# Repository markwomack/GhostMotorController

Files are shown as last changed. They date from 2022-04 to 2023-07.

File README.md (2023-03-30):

# Ghost Motor Controller
<p>The Ghost Motor Controller is currently a proof-of-concept project that is creating motor controller hardware and software to manage two BLDC hoverboard/eScooter motors with 3-phase motor encoders. The goal is to use this motor controller as part of a mobile, differential drive robot, and to have a design that can eventually be reused with different underlying hardware and motors. The parameters of the project are to use as many 'off-the-shelf' parts as possible and as few custom designed parts. This is where the project name comes from: at the end of the day we are just putting a sheet over a collection of parts and calling it a motor controller. Custom PCBs are allowed since maintaining breadboards and/or protoboards in a robot can be cumbersome and require more room than desired or needed. However, much of the PCB design is (currently) integrating existing break out boards, mostly from Pololu and Sparkfun.</p>

## Status
<p>Ghost is currently in the 'proof-of-concept' phase. Most of the time thus far has been spent choosing the initial set of parts, getting a power system in place to support the parts, and designing the first version of circuitry that will make up the motor controller. The power system, motors, and a control circuit has been designed and tested. A custom PCB has been designed and will be integrated with the test system soon.</p>

## Hardware
Instead of creating a custom circuit to control the motors, an existing eScooter controller is being used. But since this controller doesn't have a programmatic interface, a microcontroller circuit is being designed. Basically a controller of a controller. This is the Ghost Motor Controller. The hardware will support I2C, 3 RC channel inputs, and a serial port for debugging output.

## Software
The Ghost Motor Controller will provide an API accessible through I2C. Using this API the user will be able to set/get configuration and set/get information and actions on the motors and associated encoders. Everything one needs to control the motors on a mobile, differential drive robot will be provided. It will be very similar to existing APIs for other popular controllers, like the RoboClaw.

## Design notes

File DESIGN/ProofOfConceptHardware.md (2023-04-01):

# Proof of Concept Hardware (work in progress)
<p>For the proof of concept the parts below were used. If building your own version you can use
  these same parts or substitute different parts for anything in the 'Motor and Power' category
  as long as it conforms to the following requirements:</p>
  
  - The motors must be 3 phase and provide encoder signals that can be connected to the 3.3v
    Teensy 4.0 (using a 5v->3.3v logic converter, if needed, is acceptable).
  - The BLDC motor controllers must be compatible with the chosen motors and must allow for the
    speed to be set via a PWM signal.
  - Proper voltage must be provided to the motors, the motorcontrollers, and the Teensy 4.0.
  - The [36v->5v step-down regulator](https://www.amazon.com/dp/B07YCQTSXQ) is used for intial
    voltage conversion, and a second, smaller [5v step-down regulator](https://www.pololu.com/product/4941)
    is used for added protection.

<p>Substituting a different microcontroller will most likely require major reworking of the code,
  and so it is recommended that the Teensy 4.0 be used and not substituted. YMMV.</p>

## Motor and Power
  - 2 - [12" scooter/ebike BLDC motors](https://www.amazon.com/dp/B08ZXYND7G)
  - 2 - [BLDC motor controllers](https://www.amazon.com/RioRand-6-60V-Brushless-Electric-Controller/dp/B087M2378D)
  - 1 - [36v ebike lithium ion battery](https://www.amazon.com/dp/B08FWRZYJ3)
  - 1 - [Battery Disconnect Switch](https://www.amazon.com/dp/B08YXGXW2W)
  - 1 - [Inline Fuse Holder](https://www.amazon.com/dp/B081DHT8Y7)
  - 2 - [24v DC regulator](https://www.amazon.com/gp/product/B098D8HMJ9)
  - 1 - [5v DC step-down regulator](https://www.amazon.com/dp/B07YCQTSXQ)
  - 2 - [Shunt Regulator](https://www.pololu.com/product/3779)
  - 1 - [Mini Pushbutton Power Switch with Reverse Voltage Protection](https://www.pololu.com/product/2808)
  - 2 - [Big Pushbutton Power Switch with Reverse Voltage Protection](https://www.pololu.com/product/2813)
  - 1 - [3.3v step-down regulator](https://www.pololu.com/product/4940)
  - 1 - [5v step-down/up regulator](https://www.pololu.com/product/4941)
  - 1 - Diode (to prevent backflow to the power switches)
  - 1 - Momentary pushbutton

## Microcontroller
  - 1 - [Teensy 4.0](https://www.pjrc.com/store/teensy40.html)
  - 5 - [Logic Converter](https://www.sparkfun.com/products/12009)
  - 2 - [Hex Inverters with Schmitt Triggers IC chips)](https://www.digikey.com/en/products/detail/texas-instruments/SN74HC14N/277223)
  - 6 - [1000pF capacitors](https://www.digikey.com/en/products/detail/vishay-beyschlag-draloric-bc-components/A102K15X7RF5TAA/2356716)
  - 1 - Momentary pushbutton

## Miscellaneous
  - [Wire connectors](https://www.amazon.com/dp/B0882TNS73)
  - [12 AWG wire](https://www.amazon.com/dp/B01ABOPMEI)

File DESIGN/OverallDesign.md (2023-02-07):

# Overall Design
<p>Simply stated, the goal of this project is to create a motor controller that can
control two scooter Brushless DC (BLDC) motors and that can be used in robotic projects in
replacement of more typical motors and motor controllers. Scooter BLDC motors, due
to their design, can handle large loads (on the order of a grown adult) and can
provide lots of torque. These features make them very ideal for many robotic
applications.</p>

<p>BLDC motors have been around forever, and are a staple of most 
robotic projects, especially mobile robots. BLDC motors used on scooters have been
on the scene more recently but have gained in popularity and availability. One can
find many different models on Amazon and scooter supply websites. But using them
in a robotics project poses some difficulty.</p>

<p>Scooter BLDC motors use a 3-phase design for the motor, not just the simple two
wire configuration used in most robotic motors. In addition, while most scooter
motors have encoders built in, they are three encoders to match the 3-phases.
Two sensor, quadrature encoder support doesn't work. Both of these major differences
mean that none of the normal robotic motor controllers can be used to control scooter
motors.</p>

<p>While the usual stable of robotic motor controllers can't be used for scooter
BLDC motors, there are motor controllers that exist to control them. Scooters
obviously need some component to manage the motor speed, braking, and stopping
as the user drives the scooter around. These controllers are fairly simple in
design, providing for the 3-phase power signals and using the encoders to determine
wheel position and how to control the motor. As part of this project, one could design
and build such a controller from scratch, but instead we have opted to incorporate the
existing simple controller in the design. Doing so allows the builder to swap out the
simple controller to better match the power and motor requirements of their project.
As long as the replacement controller uses the same required interface for the power
and encoders, it should just be a matter of a drop-in replacement.</p>

<p>Similarly, the motors themselves can be swapped out as needed for the project
requirements. As long as the motor is a 3-phase motor with connections for power and
encoders, it will be compatible.</p>

<p>The real innovation will be the circuitry that encapsulates the simple controllers
and motors. It will provide an interface to control the motors based on a popular 
motor controller protocol, the RoboClaw. It will be a motor controller of motor
controllers, so to speak. Commands to control the motors will be sent to this top
level controller (via I2C or Serial, tbd), and the top level controller will in turn
send the proper commands to the simple controllers. In addition, PID control will be
implemented, using the 3-phase encoder signals from the motors. But putting the simple
controllers and motors behind a higher-level motor controller interface, scooter BLDC
motors will be easier to incorporate into a robotics project.</p>

# References

  - [https://www.digikey.com/en/articles/how-to-power-and-control-brushless-dc-motors](https://www.digikey.com/en/articles/how-to-power-and-control-brushless-dc-motors)
  - [https://www.digikey.com/en/blog/using-bldc-hall-sensors-as-position-encoders-part-1](https://www.digikey.com/en/blog/using-bldc-hall-sensors-as-position-encoders-part-1)

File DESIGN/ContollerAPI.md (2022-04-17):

# Controller Interface/API
This document outlines the API of the controller interface that is used to control the motors.
For purposes of design we are assuming I2C is used and that there is a set of registers that
are read-only or read/write as appropriate. Setting a register affects the motorcontroller as
it uses that value to control the motors.

## Read/Write registers

  - Target speed left motor - The target speed for the left motor the PID should aim for. (units for speed, tbd)
  - P value, left motor - The P value to use for PID controller of left motor.
  - I value, left motor - The I value to use for PID controller of left motor.
  - D value, left motor - The D value to use for PID controller of left motor.
  - Target speed right motor - The target speed for the right motor the PID should aim for. (units for speed, tbd)
  - P value, right motor - The P value to use for PID controller of right motor.
  - I value, right motor - The I value to use for PID controller of right motor.
  - D value, right motor - The D value to use for PID controller of right motor.
  - Command timeout - The amount of time before the motorcontroller will stop all motors if no command is received.

## Read-Only registers

  - Current speed left motor - The current speed of the left motor.
  - Current speed right motor - The current speed of the right motor.

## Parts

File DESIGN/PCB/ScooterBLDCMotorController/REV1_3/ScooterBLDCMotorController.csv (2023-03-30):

Comment | Designator | Footprint | LCSC
M1 OUTPUT | J1 | TerminalBlock:TerminalBlock_Altech_AK300-3_P5.00mm | C5142611
RC_ENABLE | J10 | Connector_PinHeader_2.54mm:PinHeader_1x02_P2.54mm_Vertical | C5116481
TO M2 ENCODER | J11 | Connector_JST:JST_XH_B5B-XH-A_1x05_P2.50mm_Vertical | C157991
M2 INPUT | J12 | Custom:TerminalBlock_Altech_AK300-5_P5.00mm | C395854
RC CH 3 | J15 | Connector_JST:JST_XH_B3B-XH-A_1x03_P2.50mm_Vertical | C161870
TO M1 ENCODER | J2 | Connector_JST:JST_XH_B5B-XH-A_1x05_P2.50mm_Vertical | C157991
M1 INPUT | J3 | Custom:TerminalBlock_Altech_AK300-5_P5.00mm | C395854
M2 OUTPUT | J4 | TerminalBlock:TerminalBlock_Altech_AK300-3_P5.00mm | C5142611
I2C | J5 | Connector_JST:JST_XH_B2B-XH-A_1x02_P2.50mm_Vertical | C158012
TEST SWITCH | J6 | Connector_JST:JST_XH_B2B-XH-A_1x02_P2.50mm_Vertical | C158012
RC CH 1 | J7 | Connector_JST:JST_XH_B3B-XH-A_1x03_P2.50mm_Vertical | C161870
RC CH 2 | J8 | Connector_JST:JST_XH_B3B-XH-A_1x03_P2.50mm_Vertical | C161870
RC_PWR | J9 | Connector_PinHeader_2.54mm:PinHeader_1x02_P2.54mm_Vertical | C5116481
5v | POWER1 | Connector_JST:JST_XH_B2B-XH-A_1x02_P2.50mm_Vertical | C158012
SERIAL | SERIAL1 | Connector_JST:JST_XH_B2B-XH-A_1x02_P2.50mm_Vertical | C158012
SN74HC14NR | U2,U5 | Package_DIP:DIP-14_W7.62mm | C2907

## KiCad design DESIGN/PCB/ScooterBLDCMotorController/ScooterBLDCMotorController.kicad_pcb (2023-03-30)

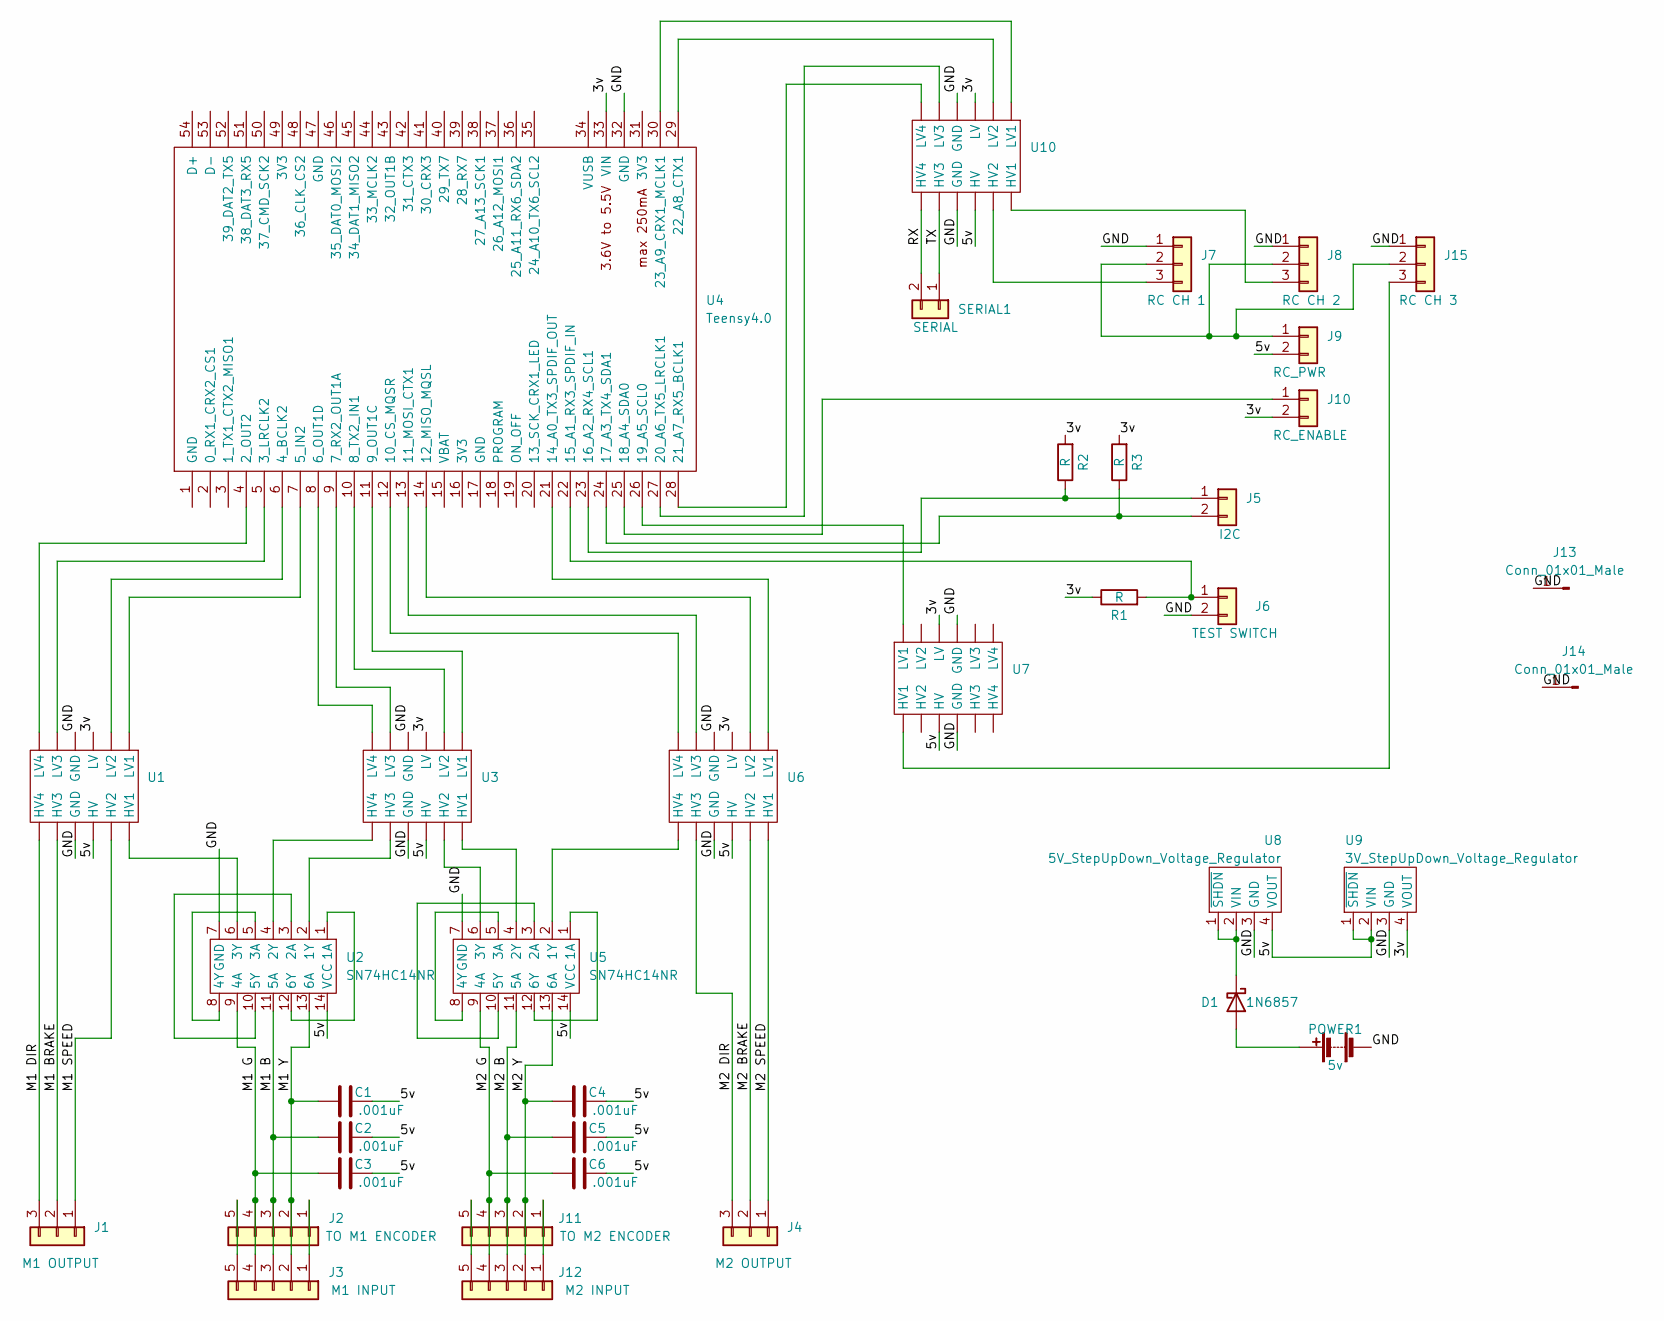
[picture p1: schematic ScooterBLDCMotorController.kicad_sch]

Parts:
C1, C2, C3, C4, C5, C6: .001uF; C_Axial_L3.8mm_D2.6mm_P7.50mm_Horizontal
D1: 1N6857; D_DO-35_SOD27_P7.62mm_Horizontal
J1: M1 OUTPUT; TerminalBlock_Altech_AK300-3_P5.00mm; LCSC C8393
J2: TO M1 ENCODER; JST_XH_B5B-XH-A_1x05_P2.50mm_Vertical; LCSC C157991
J3: M1 INPUT; TerminalBlock_Altech_AK300-5_P5.00mm; LCSC C395854
J4: M2 OUTPUT; TerminalBlock_Altech_AK300-3_P5.00mm; LCSC C8393
J5: I2C; JST_XH_B2B-XH-A_1x02_P2.50mm_Vertical; LCSC C158012
J6: TEST SWITCH; JST_XH_B2B-XH-A_1x02_P2.50mm_Vertical; LCSC C158012
J7: RC CH 1; JST_XH_B3B-XH-A_1x03_P2.50mm_Vertical; LCSC C161870
J8: RC CH 2; JST_XH_B3B-XH-A_1x03_P2.50mm_Vertical; LCSC C161870
J9: RC_PWR; PinHeader_1x02_P2.54mm_Vertical; LCSC C5116481
J10: RC_ENABLE; PinHeader_1x02_P2.54mm_Vertical; LCSC C5116481
J11: TO M2 ENCODER; JST_XH_B5B-XH-A_1x05_P2.50mm_Vertical; LCSC C157991
J12: M2 INPUT; TerminalBlock_Altech_AK300-5_P5.00mm; LCSC C395854
J13, J14: Conn_01x01_Male; PinHeader_1x01_P2.54mm_Vertical
J15: RC CH 3; JST_XH_B3B-XH-A_1x03_P2.50mm_Vertical; LCSC C161870
POWER1: 5v; JST_XH_B2B-XH-A_1x02_P2.50mm_Vertical; LCSC C158012
R1, R2, R3: R; R_Axial_DIN0204_L3.6mm_D1.6mm_P7.62mm_Horizontal
SERIAL1: SERIAL; JST_XH_B2B-XH-A_1x02_P2.50mm_Vertical; LCSC C158012
U1, U3, U6, U7, U10: Level Shifter
U2, U5: SN74HC14NR; DIP-14_W7.62mm; LCSC C2907
U4: Teensy4.0; Teensy40_sides
U8: 5V_StepUpDown_Voltage_Regulator; StepUpDown Voltage Regulator
U9: 3V_StepUpDown_Voltage_Regulator; StepUpDown Voltage Regulator

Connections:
/3v: J10.2, R1.1, R2.2, R3.2, U1.9 (LV), U3.9 (LV), U4.33 (VIN), U6.9 (LV), U7.9 (LV), U9.4 (VOUT), U10.9 (LV)
/5v: C1.2, C2.2, C3.2, C4.2, C5.1, C6.1, J9.2, U1.4 (HV), U2.14 (VCC), U3.4 (HV), U5.14 (VCC), U6.4 (HV), U7.4 (HV), U8.4 (VOUT), U9.1 (~SHDN), U9.2 (VIN), U10.4 (HV)
/GND: J6.2, J7.1, J8.1, J13.1, J14.1, J15.1, POWER1.2 (-), U1.3 (GND), U1.10 (GND), U2.7 (GND), U3.3 (GND), U3.10 (GND), U4.32 (GND), U5.7 (GND), U6.3 (GND), U6.10 (GND), U7.3 (GND), U7.10 (GND), U8.3 (GND), U9.3 (GND), U10.3 (GND), U10.10 (GND)
/M1 B: C2.1, J2.3, J3.3, U2.11 (5A)
/M1 BRAKE: J1.2, U1.2 (HV3)
/M1 DIR: J1.3, U1.1 (HV4)
/M1 G: C3.1, J2.4, J3.4, U2.9 (4A)
/M1 SPEED: J1.1, U1.5 (HV2)
/M1 Y: C1.1, J2.2, J3.2, U2.13 (6A)
/M2 B: C5.2, J11.3, J12.3, U5.11 (5A)
/M2 BRAKE: J4.2, U6.5 (HV2)
/M2 DIR: J4.3, U6.2 (HV3)
/M2 G: C6.2, J11.4, J12.4, U5.9 (4A)
/M2 SPEED: J4.1, U6.6 (HV1)
/M2 Y: C4.1, J11.2, J12.2, U5.13 (6A)
/RX: SERIAL1.2, U10.1 (HV4)
/TX: SERIAL1.1, U10.2 (HV3)
unnamed: D1.2 (A), POWER1.1 (+)
unnamed: D1.1 (K), U8.1 (~SHDN), U8.2 (VIN)
unnamed: J2.1, J3.1
unnamed: J2.5, J3.5
unnamed: J5.1, R2.1, U4.23 (16_A2_RX4_SCL1)
unnamed: J5.2, R3.1, U4.24 (17_A3_TX4_SDA1)
unnamed: J6.1, R1.2, U4.22 (15_A1_RX3_SPDIF_IN)
unnamed: J7.3, U10.5 (HV2)
unnamed: J8.3, U10.6 (HV1)
unnamed: J10.1, U4.25 (18_A4_SDA0)
unnamed: J11.1, J12.1
unnamed: J11.5, J12.5
unnamed: J7.2, J8.2, J9.1, J15.2
unnamed: J15.3, U7.6 (HV1)
unnamed: U1.6 (HV1), U2.6 (3Y)
unnamed: U1.7 (LV1), U4.7 (5_IN2)
unnamed: U1.8 (LV2), U4.6 (4_BCLK2)
unnamed: U1.11 (LV3), U4.5 (3_LRCLK2)
unnamed: U1.12 (LV4), U4.4 (2_OUT2)
unnamed: U2.1 (1A), U2.12 (6Y)
unnamed: U2.2 (1Y), U3.2 (HV3)
unnamed: U2.3 (2A), U2.10 (5Y)
unnamed: U2.4 (2Y), U3.1 (HV4)
unnamed: U2.5 (3A), U2.8 (4Y)
unnamed: U3.6 (HV1), U5.4 (2Y)
unnamed: U3.5 (HV2), U5.6 (3Y)
unnamed: U3.7 (LV1), U4.11 (9_OUT1C)
unnamed: U3.8 (LV2), U4.10 (8_TX2_IN1)
unnamed: U3.11 (LV3), U4.9 (7_RX2_OUT1A)
unnamed: U3.12 (LV4), U4.8 (6_OUT1D)
unnamed: U4.12 (10_CS_MQSR), U6.12 (LV4)
unnamed: U4.13 (11_MOSI_CTX1), U6.11 (LV3)
unnamed: U4.14 (12_MISO_MQSL), U6.8 (LV2)
unnamed: U4.21 (14_A0_TX3_SPDIF_OUT), U6.7 (LV1)
unnamed: U4.26 (19_A5_SCL0), U7.7 (LV1)
unnamed: U5.1 (1A), U5.12 (6Y)
unnamed: U5.2 (1Y), U6.1 (HV4)
unnamed: U5.3 (2A), U5.10 (5Y)
unnamed: U5.5 (3A), U5.8 (4Y)
unnamed: U4.30 (23_A9_CRX1_MCLK1), U10.7 (LV1)
unnamed: U4.29 (22_A8_CTX1), U10.8 (LV2)
unnamed: U4.27 (20_A6_TX5_LRCLK1), U10.11 (LV3)
unnamed: U4.28 (21_A7_RX5_BCLK1), U10.12 (LV4)

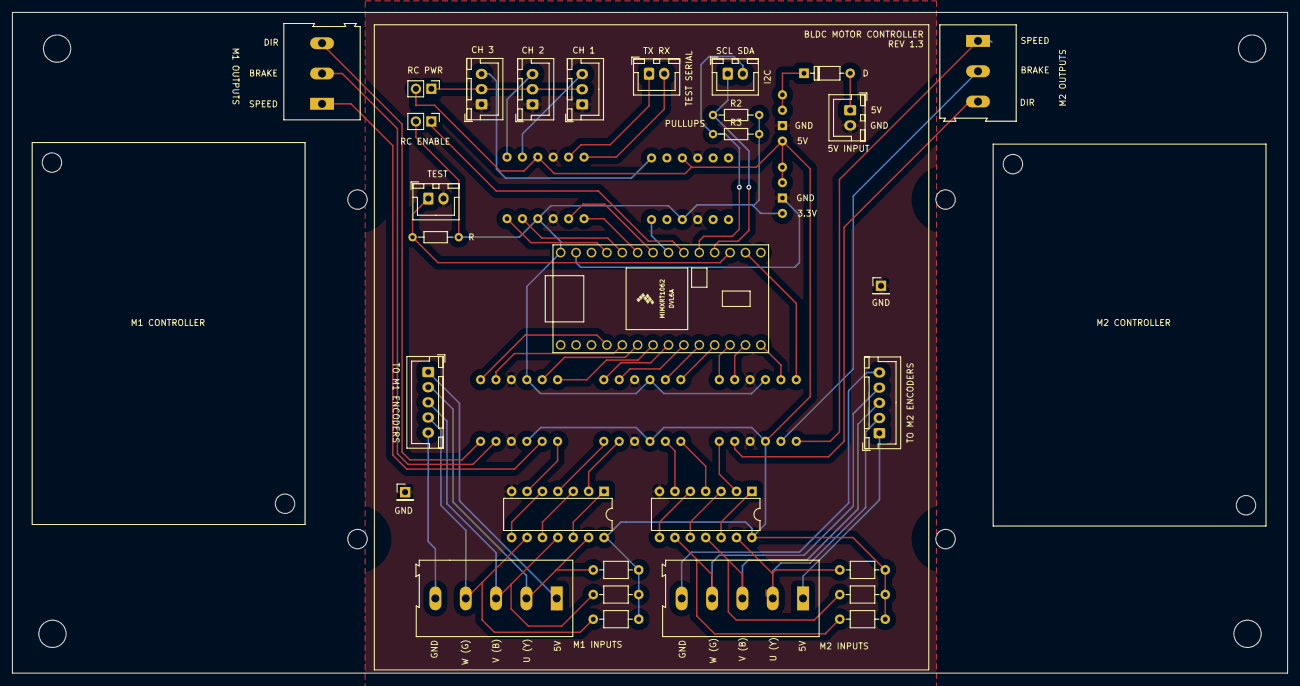
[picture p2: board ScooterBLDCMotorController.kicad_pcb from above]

Board: 2 copper layers, 210.3 x 109.0 mm, 37 parts (0 on the bottom side), 60 nets.

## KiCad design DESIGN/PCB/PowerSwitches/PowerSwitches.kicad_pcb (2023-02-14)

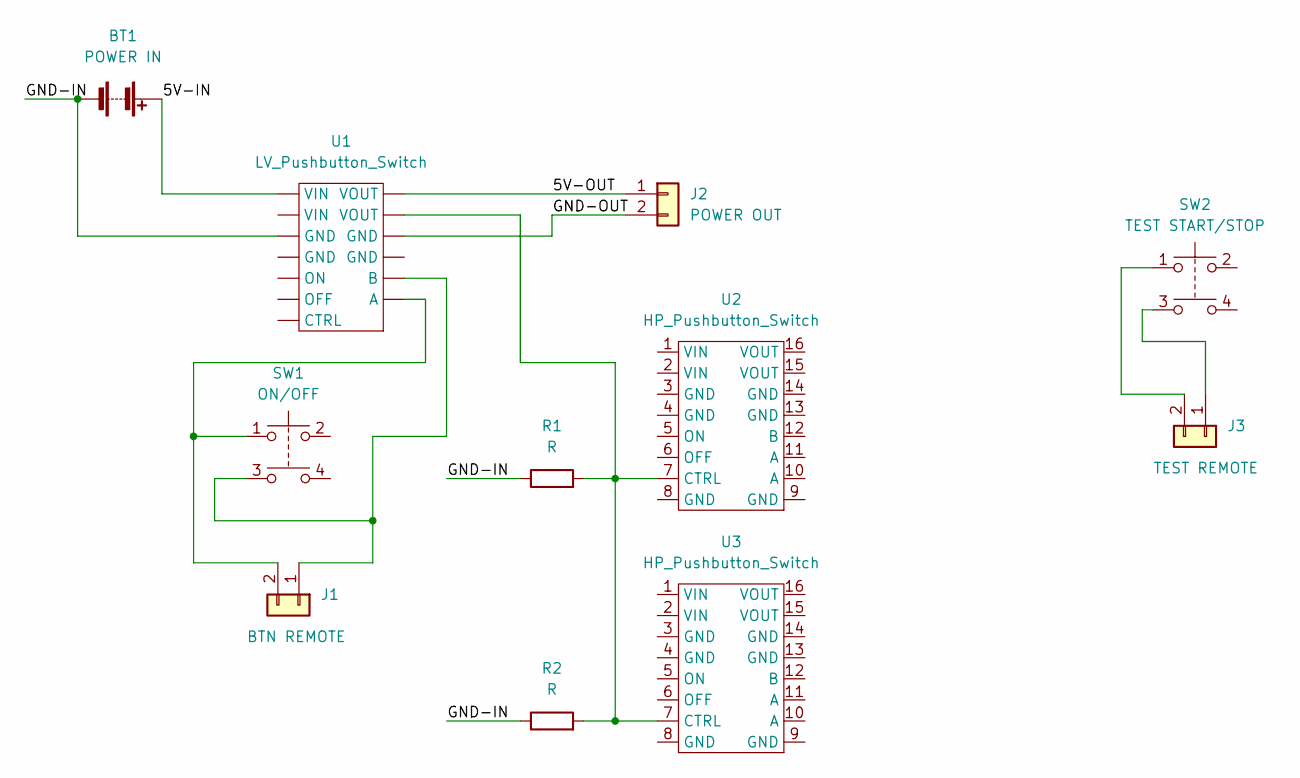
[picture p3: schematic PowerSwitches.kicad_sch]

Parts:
BT1: POWER IN; JST_XH_B2B-XH-A_1x02_P2.50mm_Vertical
J1: BTN REMOTE; JST_XH_B2B-XH-A_1x02_P2.50mm_Vertical
J2: POWER OUT; JST_XH_B2B-XH-A_1x02_P2.50mm_Vertical
J3: TEST REMOTE; JST_XH_B2B-XH-A_1x02_P2.50mm_Vertical
R1, R2: R; R_Axial_DIN0207_L6.3mm_D2.5mm_P7.62mm_Horizontal
SW1: ON/OFF; Small Dual Push Button
SW2: TEST START/STOP; Small Dual Push Button
U1: LV_Pushbutton_Switch; LV_PushButton_Switch
U2, U3: HP_Pushbutton_Switch; HV_PushButton_Switch

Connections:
/5V-IN: BT1.1 (+), U1.1 (VIN)
/5V-OUT: J2.1, U1.13 (VOUT)
/GND-IN: BT1.2 (-), R1.1, R2.1, U1.3 (GND)
/GND-OUT: J2.2, U1.11 (GND)
unnamed: J1.2, SW1.1, U1.8 (A)
unnamed: J3.2, SW2.1
unnamed: R1.2, R2.2, U1.12 (VOUT), U2.7 (CTRL), U3.7 (CTRL)
unnamed: J3.1, SW2.3
unnamed: J1.1, SW1.3, U1.9 (B)

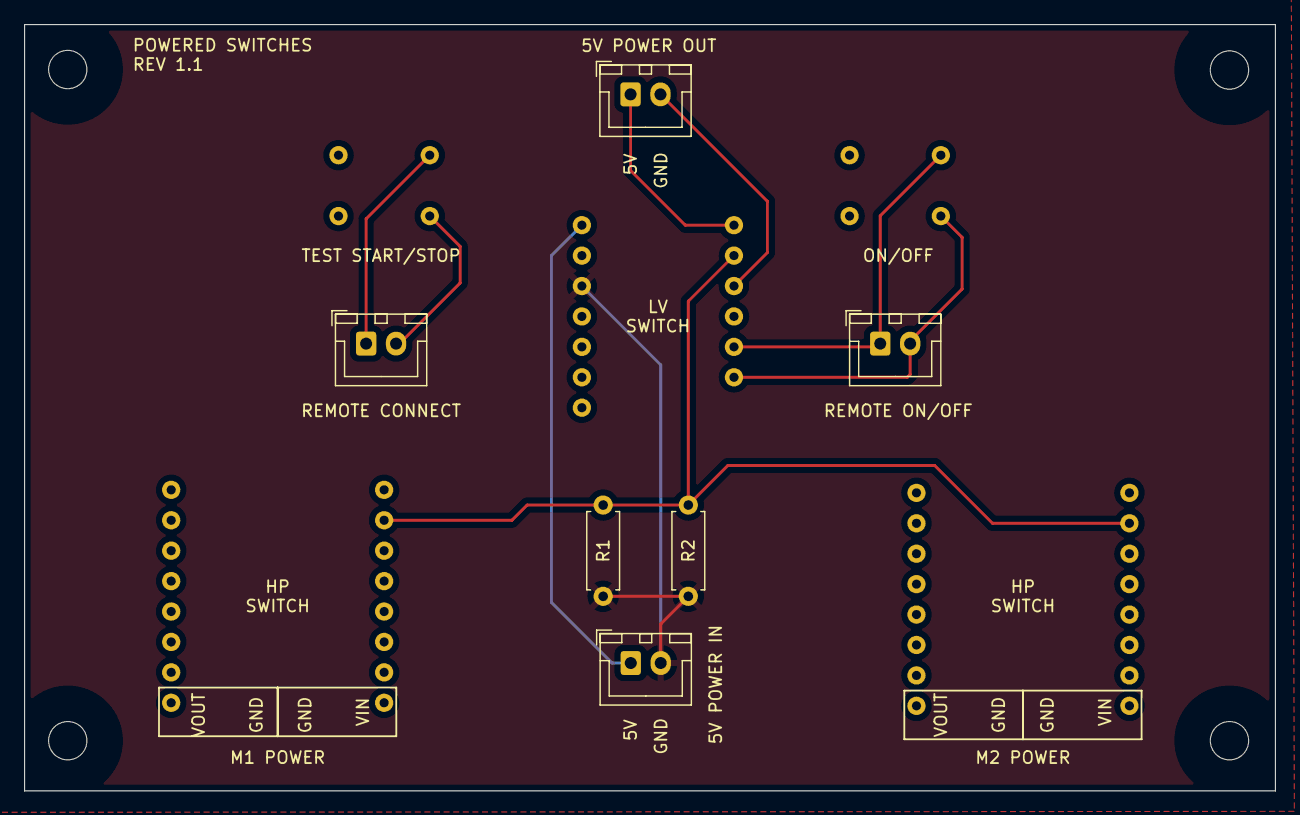
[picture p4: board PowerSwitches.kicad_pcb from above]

Board: 2 copper layers, 104.4 x 64.0 mm, 11 parts (0 on the bottom side), 9 nets.

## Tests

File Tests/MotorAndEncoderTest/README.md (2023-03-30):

# BLDCTest
<p>This is a sketch that is used to test the proof-of-concept electronics for one or two motors.
If only using one motor, as the system is built out, then comment out the motor M1 tasks that
are defined and setup in the sketch.</p>

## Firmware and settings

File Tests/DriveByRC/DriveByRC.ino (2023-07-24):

//
// Licensed under Apache 2.0 license.
// See accompanying LICENSE file for details.
//

// This is a program to drive a MotorController
// instance using input from the RC channels.

// Arduino includes
#include <Arduino.h>

// Third Party includes
#include <DebugMsgs.h>               // https://github.com/markwomack/ArduinoLogging
#include <TaskManager.h>             // https://github.com/markwomack/TaskManager
#include <BlinkTask.h>
#include <MotorAndEncoderManager.h>  // https://github.com/markwomack/MotorAndEncoderManager
#include <MotorController.h>         // https://github.com/markwomack/MotorAndEncoderManager
#include <GhostMotorManager.h>
#include <ThreePhaseMotorEncoder.h>
#include <RampedMotorPID.h>
#include <CheckForSerialUpdateTask.h>
#include <FlasherXUpdater.h>

// Local includes
#include "globals.h"
#include "pin_assignments.h"
#include "ReadFromRCTask.h"
#include "AdjustSpeedsTask.h"
#include "MeasureSpeedTask.h"

// Motor manager
MotorAndEncoderManager* motorManager;

// Motor Controller
MotorController* motorController;

#define SERIAL_BUFFER_SIZE 8192
uint8_t incomingBuffer[SERIAL_BUFFER_SIZE];
uint8_t outgoingBuffer[SERIAL_BUFFER_SIZE];

ReadFromRCTask readFromRCTask;
AdjustSpeedsTask adjustSpeedsTask;
MeasureSpeedTask measureSpeedTask;
CheckForSerialUpdateTask checkForSerialUpdateTask(&Serial5);

void setup() {
  Serial.begin(115200);
  Serial5.begin(115200);
  Serial5.addMemoryForRead(incomingBuffer, SERIAL_BUFFER_SIZE);
  Serial5.addMemoryForWrite(outgoingBuffer, SERIAL_BUFFER_SIZE);
  delay(1000); // Give serials a chance to catch up

  // Comment out to disable debug output
  DebugMsgs.enableLevel(DEBUG);

  // All output now goes to Serial5
  DebugMsgs.setPrintWrapper(new PrintWrapper(&Serial5));

  DebugMsgs.debug().println("Starting Drive By RC");
  
  pinMode(RC_ENABLE_PIN, INPUT);
  if (digitalRead(RC_ENABLE_PIN) == LOW) {
    DebugMsgs.debug().println("RC IS NOT ENABLED, exiting");
    DebugMsgs.flush();
    exit(0);
  }
  
  // RC Channel inputs
  pinMode(RC_CH1_PIN, INPUT);
  pinMode(RC_CH2_PIN, INPUT);
  pinMode(RC_CH3_PIN, INPUT);

  // Setup the encoders
  ThreePhaseMotorEncoder* m0ThreePhaseEncoder = new ThreePhaseMotorEncoder();
  m0ThreePhaseEncoder->begin(M0_V_SIGNAL_PIN, M0_W_SIGNAL_PIN, M0_U_SIGNAL_PIN);
  ThreePhaseMotorEncoder* m1ThreePhaseEncoder = new ThreePhaseMotorEncoder();
  m1ThreePhaseEncoder->begin(M1_V_SIGNAL_PIN, M1_W_SIGNAL_PIN, M1_U_SIGNAL_PIN);

  // Setup the motor manager
  GhostMotorManager* ghostMotorManager = new GhostMotorManager();
  ghostMotorManager->begin(M0_SPEED_PIN, M0_DIR_PIN, M0_BRAKE_PIN,
  M1_SPEED_PIN, M1_DIR_PIN, M1_BRAKE_PIN);
  motorManager = (MotorAndEncoderManager*)ghostMotorManager;
  motorManager->setEncoders(m0ThreePhaseEncoder, m1ThreePhaseEncoder);

  // Should MAX_SPEED_INCREMENT_ALLOWED be adjusted to the frequency adjustSpeedsTask will be called?
  MotorPID* m0MotorPID = new RampedMotorPID(MAX_SPEED_INCREMENT_ALLOWED);
  MotorPID* m1MotorPID = new RampedMotorPID(MAX_SPEED_INCREMENT_ALLOWED);
  
  // Create the motor controller
  motorController = new MotorController(motorManager, m0MotorPID, m1MotorPID, 50, RADIANS_PER_TICK, MAX_RADIANS_PER_SECOND);

  DebugMsgs.debug().print("RADIANS_PER_TICK: ").println(RADIANS_PER_TICK);
  DebugMsgs.debug().print("MAX_RADIANS_PER_SECOND: ").println(MAX_RADIANS_PER_SECOND);
  DebugMsgs.debug().print("MAX_LINEAR_VELOCITY_ALLOWED: ").println(MAX_LINEAR_VELOCITY_ALLOWED);
  DebugMsgs.debug().print("MAX_ANGULAR_VELOCITY_ALLOWED: ").println(MAX_ANGULAR_VELOCITY_ALLOWED);
  DebugMsgs.debug().print("MAX_SPEED_INCREMENT_ALLOWED: ").println(MAX_SPEED_INCREMENT_ALLOWED);
  
  // Set the RC pins into the readFromRCTask
  readFromRCTask.setRCPins(RC_CH1_PIN, RC_CH2_PIN, -1);

  // Set the needed references into the adjustSpeedsTask
  adjustSpeedsTask.setMotorManagerAndController(motorManager, motorController);
  adjustSpeedsTask.setReadFromRCTask(&readFromRCTask);

  measureSpeedTask.setMotorAndEncoderManager(motorManager);

  // Set up the task manager with idle tasks
  taskManager.addIdleBlinkTask(100);
  taskManager.addIdleTask(&checkForSerialUpdateTask, 1000);

  // Set up the task manager with regular tasks
  taskManager.addBlinkTask(500);
  taskManager.addTask(&readFromRCTask, 50);
  taskManager.addTask(&adjustSpeedsTask, 50);
  //taskManager.addTask(&measureSpeedTask, 500);
  taskManager.addTask(&checkForSerialUpdateTask, 1000);

  // Wait for the user to press the button to start
  taskManager.startMonitoringButton(BUTTON_PIN, HIGH);
}

void loop() {
  taskManager.update();
  
  // If there is an firmware update, stop everything and process
  if (checkForSerialUpdateTask.updateIsAvailable()) {
    DebugMsgs.debug().println("Firmware update available, processing...");

    // stop normal operation
    taskManager.stop();

    // Give some flexibility on receiving update data
    FlasherXUpdater::setTimeout(500);
    
    // perform the firmware update
    FlasherXUpdater::performUpdate(checkForSerialUpdateTask.getUpdateStream());

    // bleed any remaining update data
    DebugMsgs.debug().println("Firmware update aborted, clearing remaining update data");
    Stream* updateStream = checkForSerialUpdateTask.getUpdateStream();
    uint32_t lastRead = millis();
    while (millis() < lastRead + 500) {
      if (updateStream->available()) {
        uint8_t buffer[4096];
        updateStream->readBytes(buffer, sizeof(buffer));
        lastRead = millis();
      }
    }

    // update aborted, restart task manager
    DebugMsgs.debug().println("Firmware update aborted, restarting normal operations");
    taskManager.startMonitoringButton(BUTTON_PIN, HIGH);
  }
}

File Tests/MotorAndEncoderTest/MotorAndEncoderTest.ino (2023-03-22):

//
// Licensed under Apache 2.0 license.
// See accompanying LICENSE file for details.
//

// This is a test program that can be used to test the connections
// to the motor controller and motor encoder hardware. It doesn't use
// any pre-built libraries to interface with the controller or encoders,
// everything is done directly to aid in debugging. From this program
// you can add tasks to drive the motors forward and reverse, print the
// tick and fault counts from the motor encoders, calculate the speed
// in tick/second, or determine how many ticks/revolution your particular
// motors support. Ideally, after using these tasks you will know:
//   1) How many ticks per/revolution
//   2) That your motor encoders are not experiencing widespread faults
//      (though faults recorded when motors are switching directions is
//      acceptable)
//   3) The ticks/second when the motors are at full power.
// You can comment out code related to motor M1 or M0 if you want to work
// with a single motor for debugging.
//
// This sketch assumes there is a momentary push button connected to BUTTON_PIN
// and that it is by default connected HIGH (and will go LOW when pressed).
// Pressing the button will start/stop the tasks.

// Arduino includes
#include <Arduino.h>
#include <inttypes.h>

// My includes
#include <DebugMsgs.h>   // https://github.com/markwomack/ArduinoLogging
#include <TaskManager.h> // https://github.com/markwomack/TaskManager
#include <Task.h>

// Local includes
#include "pin_assignments.h"
#include "globals.h"
#include "interrupts.h"
#include "tasks.h"

ControlMotorTask controlM0Task;
ControlMotorTask controlM1Task;
PrintMotorTickCountsTask printM0TickCountsTask;
PrintMotorTickCountsTask printM1TickCountsTask;
CountRotationsTask countM0RotationsTask;
PrintTickSpeedTask printTickSpeedTask;

BlinkTask idleTask;

void setupPins() {
  // Setup PWM pins, set to 0
  pinMode(M0_SPEED_PIN, OUTPUT);
  analogWrite(M0_SPEED_PIN, 0);
  pinMode(M1_SPEED_PIN, OUTPUT);
  analogWrite(M1_SPEED_PIN, 0);

  // Teensy 4.1 specific
  // Values will be 0-8191
  analogWriteResolution(13);
  analogWriteFrequency(M0_SPEED_PIN, 18310.55);
  analogWriteFrequency(M1_SPEED_PIN, 18310.55);

  // Teensy 3.5 specific 
  // Values will be 0-4095
//  analogWriteResolution(12);
//  analogWriteFrequency(M0_SPEED_PIN, 14648.437);
//  analogWriteFrequency(M1_SPEED_PIN, 14648.437);

  // Setup brake pins, engage brake
  pinMode(M0_BRAKE_PIN, OUTPUT);
  digitalWrite(M0_BRAKE_PIN, HIGH);
  pinMode(M1_BRAKE_PIN, OUTPUT);
  digitalWrite(M1_BRAKE_PIN, HIGH);

  // Setup direction pins, set for forward
  pinMode(M0_DIR_PIN, OUTPUT);
  digitalWrite(M0_DIR_PIN, LOW);
  pinMode(M1_MOTOR_DIR_PIN, OUTPUT);
  digitalWrite(M1_MOTOR_DIR_PIN, LOW);

  // Set interrupt pins for M0
  pinMode(M0_U_SIGNAL_PIN, INPUT_PULLDOWN);
  motorM0.prevUVal = digitalRead(M0_U_SIGNAL_PIN);
  attachInterrupt(M0_U_SIGNAL_PIN, countM0UTick, CHANGE);
  
  pinMode(M0_V_SIGNAL_PIN, INPUT_PULLDOWN);
  motorM0.prevVVal = digitalRead(M0_V_SIGNAL_PIN);
  attachInterrupt(M0_V_SIGNAL_PIN, countM0VTick, CHANGE);
  
  pinMode(M0_W_SIGNAL_PIN, INPUT_PULLDOWN);
  motorM0.prevWVal = digitalRead(M0_W_SIGNAL_PIN);
  attachInterrupt(M0_W_SIGNAL_PIN, countM0WTick, CHANGE);

  // Set interrupt pins for M1
  pinMode(M1_U_SIGNAL_PIN, INPUT_PULLDOWN);
  motorM1.prevUVal = digitalRead(M1_U_SIGNAL_PIN);
  attachInterrupt(M1_U_SIGNAL_PIN, countM1UTick, CHANGE);
  
  pinMode(M1_V_SIGNAL_PIN, INPUT_PULLDOWN);
  motorM1.prevVVal = digitalRead(M1_V_SIGNAL_PIN);
  attachInterrupt(M1_V_SIGNAL_PIN, countM1VTick, CHANGE);
  
  pinMode(M1_W_SIGNAL_PIN, INPUT_PULLDOWN);
  motorM1.prevWVal = digitalRead(M1_W_SIGNAL_PIN);
  attachInterrupt(M1_W_SIGNAL_PIN, countM1WTick, CHANGE);
}

void setup() {
  Serial.begin(9600);
  // give serial some time to catch up
  delay(1000);

  // Comment out to disable all debug messages
  DebugMsgs.enableLevel(DEBUG);

  setupPins();

  taskManager.addIdleTask(&idleTask, 100);
  taskManager.addBlinkTask(500);

  // If you only have one motor, you can comment out
  // the motor tasks for the other motor.
  
  // Motor M0 control and count tasks
  controlM0Task.setup(&motorM0, "M0", M0_SPEED_PIN, M0_DIR_PIN, M0_BRAKE_PIN);
  taskManager.addTask(&controlM0Task, 500);
  printM0TickCountsTask.setup(&motorM0, "M0");
  taskManager.addTask(&printM0TickCountsTask, 1000);
  
  // Motor M1 control and count tasks
  controlM1Task.setup(&motorM1, "M1", M1_SPEED_PIN, M1_MOTOR_DIR_PIN, M1_BRAKE_PIN);
  taskManager.addTask(&controlM1Task, 500);
  printM1TickCountsTask.setup(&motorM1, "M1");
  taskManager.addTask(&printM1TickCountsTask, 1000);

  // Task to help estimate ticks/rotation
  // countM0RotationsTask.setRotations(5);
  // taskManager.addTask(&countM0RotationsTask, 1);

  // Task to print motor speeds
  taskManager.addTask(&printTickSpeedTask, 1000);

  // Wait for the user to press the button to start
  taskManager.startMonitoringButton(BUTTON_PIN, HIGH);
}

void loop() {
  // put your main code here, to run repeatedly:
  taskManager.update();
}

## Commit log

2022-04-16 Added BLDCTest sketch
2023-01-01 Added com comments to match the board labeling.
2023-01-02 Used constant for button pin.
2023-01-02 Added spec images for BLDC controller
2023-01-02 Switched pin assignments
    Switched pin assignments so that they work across all of the Teensy versions.
    Added some TODO comments.
2023-01-07 Added fault counts instead of debug messages in the interrupts
2023-01-16 Updated battery switch listing
2023-01-31 Updated to latest motor design, upgraded to new task manager.
2023-02-01 Major cleanup, code for both motors to read encoders and run
2023-02-04 changed pin assignments, added some test code
2023-02-05 Added more pins for RC, Serial, and I2C. KiCAD design.
    [ScooterBLDCMotorController.kicad_pcb, ScooterBLDCMotorController.kicad_sch]
2023-02-06 Latest PCB and Rev1.0 release
    [PowerSwitches-B_Cu.gbl, PowerSwitches-B_Mask.gbs, PowerSwitches-B_Paste.gbp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]
2023-02-06 Added sketch for controlling motors via RC input
2023-02-06 Updated pin assignments
2023-02-07 Implemented sketch to use RC channels to drive motors
2023-02-07 Working version of BLDCWithRCTest
2023-02-14 Rev 1.1 of power switch pcb.
    [PowerSwitches-B_Cu.gbl, PowerSwitches-B_Mask.gbs, PowerSwitches-B_Paste.gbp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]
2023-02-25 Fixed swapped connections on level shifter.
    [ScooterBLDCMotorController-B_Cu.gbl, ScooterBLDCMotorController-B_Mask.gbs, ScooterBLDCMotorController-B_Paste.gbp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]
2023-03-05 Revision 1.2 of MotorController board
    [ScooterBLDCMotorController-B_Cu.gbl, ScooterBLDCMotorController-B_Mask.gbs, ScooterBLDCMotorController-B_Paste.gbp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]
2023-03-17 Updated PCB to use terminals, added new DriveByRC code
    [ScooterBLDCMotorController.kicad_pcb, ScooterBLDCMotorController.kicad_sch]
2023-03-18 Compile fixes, debugging in process
    [DriveByRC.ino]
2023-03-21 Fixes to get back to working version
    [MotorAndEncoderTest.ino, interrupts.cpp, tasks.cpp]
2023-03-21 Add option to run in single direction with no oscillation
    [tasks.cpp]
2023-03-27 Made PID control optional
2023-03-30 Revision 1.3 for PCB
    [ScooterBLDCMotorController-B_Cu.gbl, ScooterBLDCMotorController-B_Mask.gbs, ScooterBLDCMotorController-B_Paste.gbp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]
2023-05-03 Lots of changes to separate RC from speed control, and support MotorController vs MotorManager execution
2023-05-22 Changes to get OTA updates to work correctly
    [DriveByRC.ino, ExternalConnection.ino]
